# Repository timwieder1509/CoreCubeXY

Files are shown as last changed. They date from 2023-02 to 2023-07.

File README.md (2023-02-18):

# CoreCubeXY

### CoreCubeXY is a cheap and accessible Core-XY 3D printer

CoreCubeXY_rev2_v1_2023-Feb-13_05-33-34PM-000_CustomizedView17078552254_png

# Features:

Price: 250€-300€

All parts can be printed in PLA

Speeds of up to 300mm/s

Accelerations of up to 10000mm/s^2

Sensorless Homing when using TMC-Drivers  

Klicky_Probe compatible

Easy to upgrade 

tempImageiDoiUQ

Video of it printing a Benchy: https://youtu.be/joYZc8ANMAQ

***Note***

The 2020 extrusions I used are NUT 5 extrusions, that means that their slots are 5mm wide unlike on the more commonly on 3D printers used V-slot extrusions that have 6mm wide slots. 
You can use V-slot extrusions when you build one for yourself, use whatever is more easy for you to source. 
Just make sure that the hole in the middle of the profile has the correct diameter to cut an M5 thread into it. 

### ***Please note that this project is still a work in progress***

#### Coming Soon:

_A partlist/BOM_

_I'm already working on an alternative version with a single Z-Motor and mounts for conventional End-stops to make the build even more aproachable_

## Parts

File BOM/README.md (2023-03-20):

## Consider using the links provided in the BOM when you are building your own printer.
## That way you can support me without paying more. 
## Thanks ;)

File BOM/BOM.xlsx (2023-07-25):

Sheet: Printed Parts
3D Printed Parts
Part | amount | support needed
2xLM8UU_Mount_L | 1x | X
2xLM8UU_Mount_R | 1x
Idler_Mount_L | 1x
Idler_Mount_R | 1x
Motor_Mount_L | 1x | X
Motor_Mount_R | 1x | X
TR8_Mount | 2x
Z_Motor_Mount | 2x
AB_SB mount | 1x
Bed_Mount | 4x
Bed_Screw | 4x
Bed_Screw_Holder | 4x
Belt_Clamp | 1x
CCXY_Logo | 2x
Fan_Duct | 1x | X
Spacer | 4x
Foot | 4x
Gantry_Mount_L | 1x
Gantry_Mount_R | 1x
Hotend_Body | 1x | X
Klicky-Dock_Mount | 1x
Rod_Mount_bottom | 2x
Board_Mount | 1x
Rod_Mount_top | 2x

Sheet: Bought Parts
Bought Parts
Part | Amount | Link
Nema 17 Stepper Motor | 5x | https://bit.ly/42otSue
LM8UU | 4x | https://bit.ly/40k2tbb
SKR Mini E3 V2 | 1x | https://bit.ly/40mnx0S
GT2 Pulley | 2x | https://bit.ly/400JOBg
GT2 Idler | 10x | https://bit.ly/3FBs3QO
Mk8 Extruder | 1x | https://bit.ly/3n3rJEb
M5 x 8 | 50x | https://bit.ly/3yOAHbd
M3 x 25 | 50x | https://bit.ly/3lkwgSp
M3 x 8 | 50x | https://bit.ly/40jVfnr
M5 Hex-Nut | 10x
M3 Hex-Nut | 10x
M5 x 25 | 10x | https://bit.ly/3mTCXuP
M5 x 35 | 10x | https://bit.ly/403wvjG
Bondtech Extruder | 1x | https://bit.ly/40cFCyo
Linear shafts 8x200mm | 2x | https://bit.ly/3TupwO7
TR8 x 200 | 2x | https://bit.ly/3n7q8x0
4020 24v Fan | 1x | https://bit.ly/40g3odf
3010 24v Fan | 1x | https://bit.ly/3LDnOIE
5x8mm Shaft Coupler | 2x | https://bit.ly/40cGpPS
MGN9H (min 200mm/ max 250mm) | 2x | https://bit.ly/3JRuHEC
MGN12C 200mm | 1x | https://bit.ly/42mOvqO
Glas Bed 180x180 | 1x | https://bit.ly/40n2dIe
24v powersupply | 1x | https://bit.ly/401JMJF
M3 Heatset inserts | 20-30x | https://bit.ly/42sLghJ
255mm 2020 Extrusion | 12x | myaluprofil - Aluminum profile 20x20 Groove 5 I-Type (https://www.myaluprofil.de/product_info.php?no_boost=1)
180mm 2020 Extrusion | 4 | myaluprofil - Aluminum profile 20x20 Groove 5 I-Type (https://www.myaluprofil.de/product_info.php?no_boost=1)
M3 T-nuts | 40x | https://bit.ly/3qbo0WZ
M5 T-nuts | 40x | https://bit.ly/44A0dPw

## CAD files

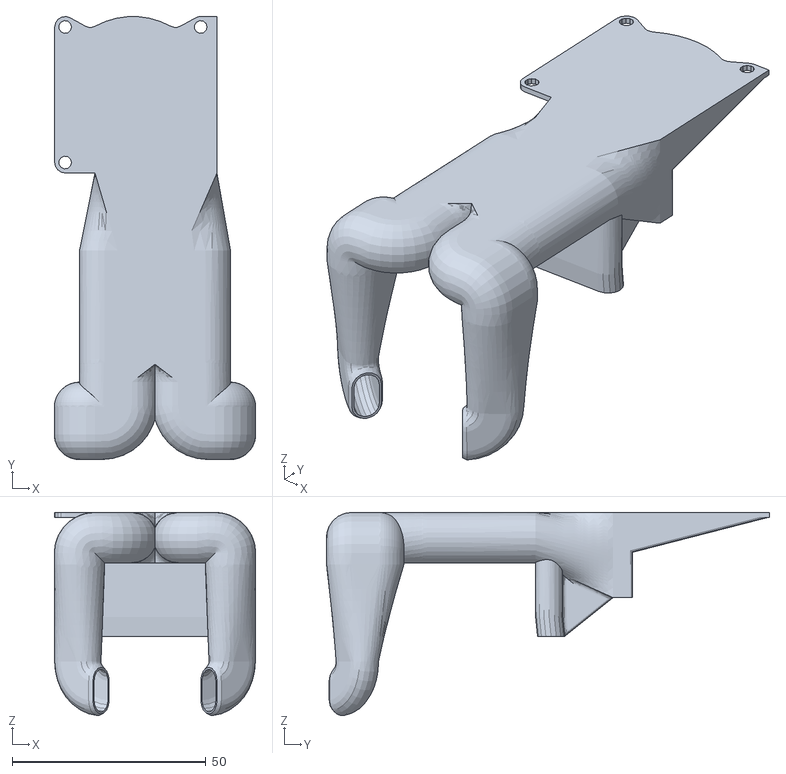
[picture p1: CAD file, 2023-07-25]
STL/Fan_Duct_v2.stl
52.0 x 114.4 x 52.5

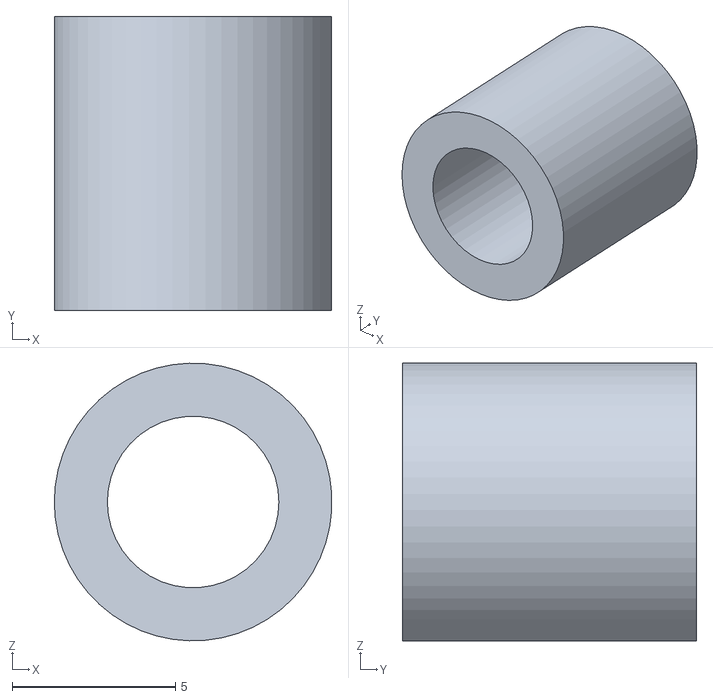
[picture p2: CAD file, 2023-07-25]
STL/Spacer.stl
8.49 x 9.00 x 8.50

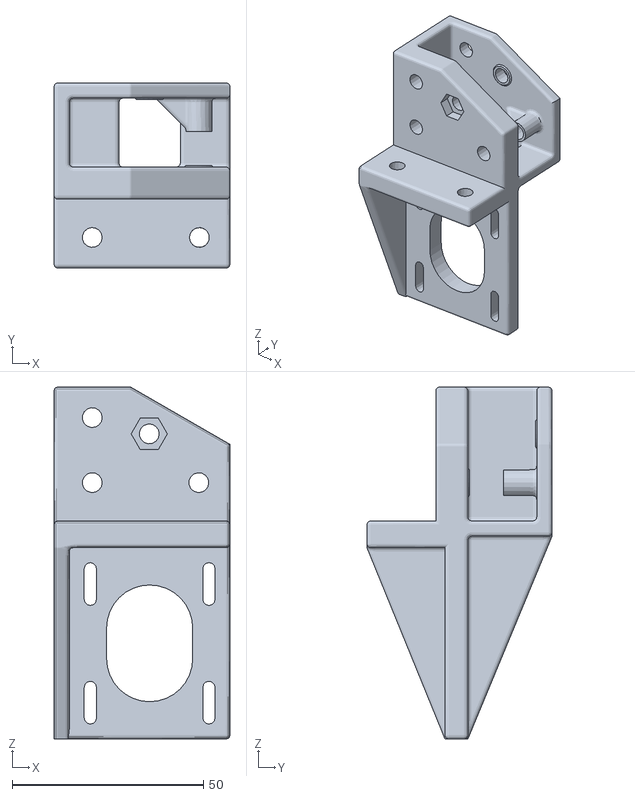
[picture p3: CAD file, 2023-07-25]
STL/Motor_Mount_L.stl
46.0 x 48.4 x 92.0

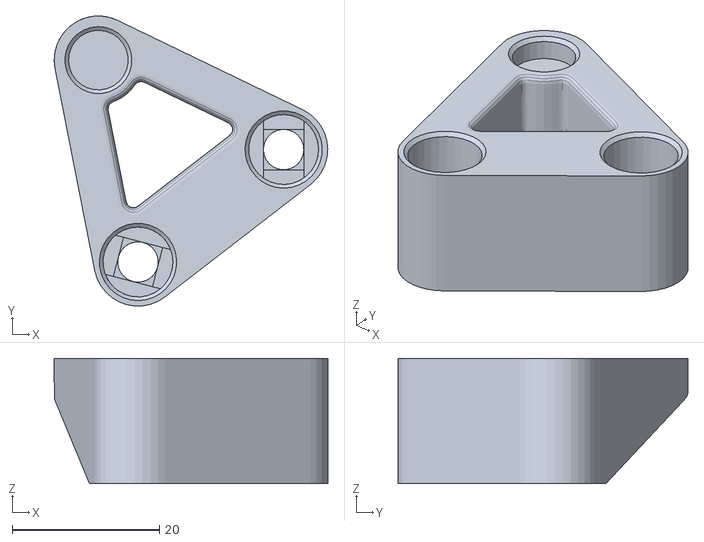
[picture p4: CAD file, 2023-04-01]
STL/Rod_Mount_bottom.stl
37.2 x 39.4 x 17.0

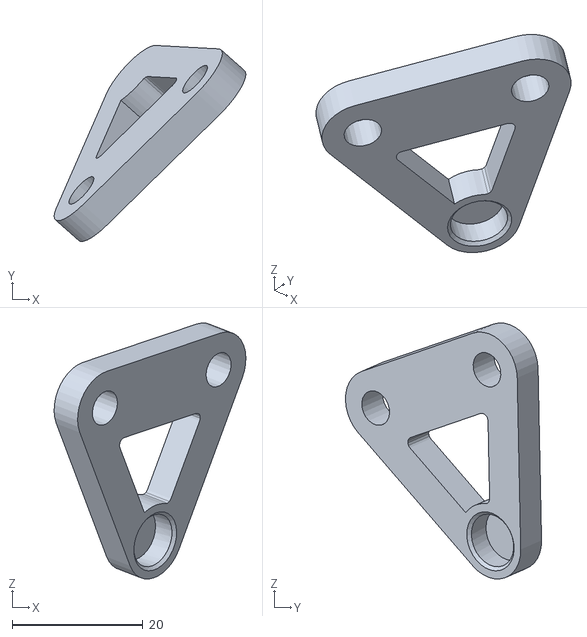
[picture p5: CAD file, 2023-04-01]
STL/Rod_Mount_top.stl
29.3 x 30.0 x 39.1

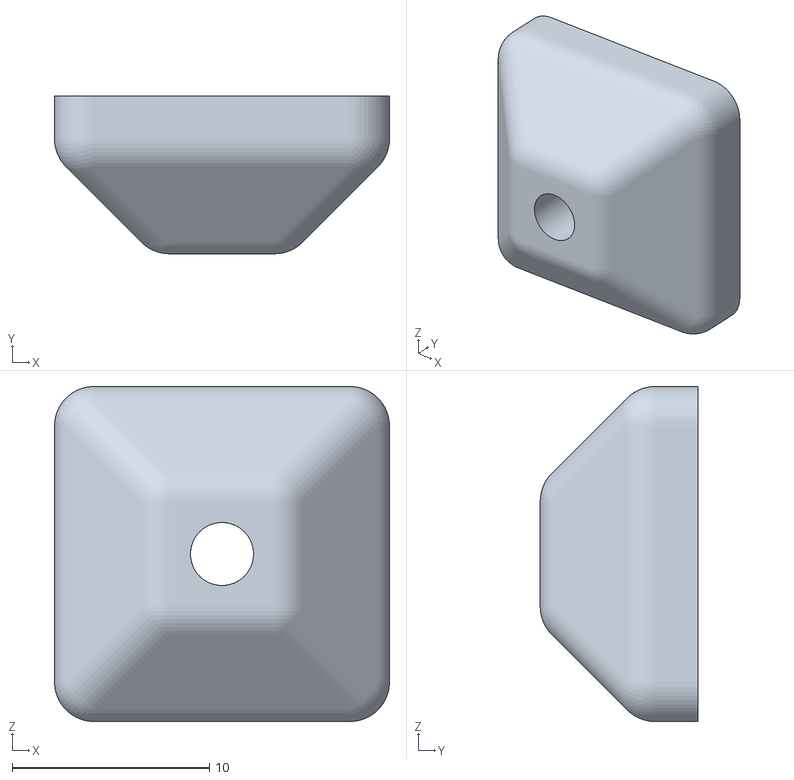
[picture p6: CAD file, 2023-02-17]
STL/Bed_Mount.stl
17.0 x 8.00 x 17.0

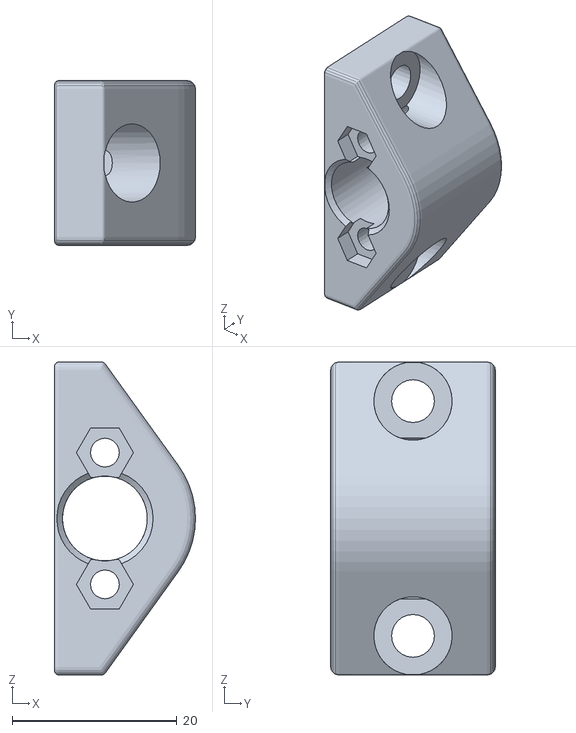
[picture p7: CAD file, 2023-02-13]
STL/TR8_Mount.stl
17.1 x 20.0 x 38.0

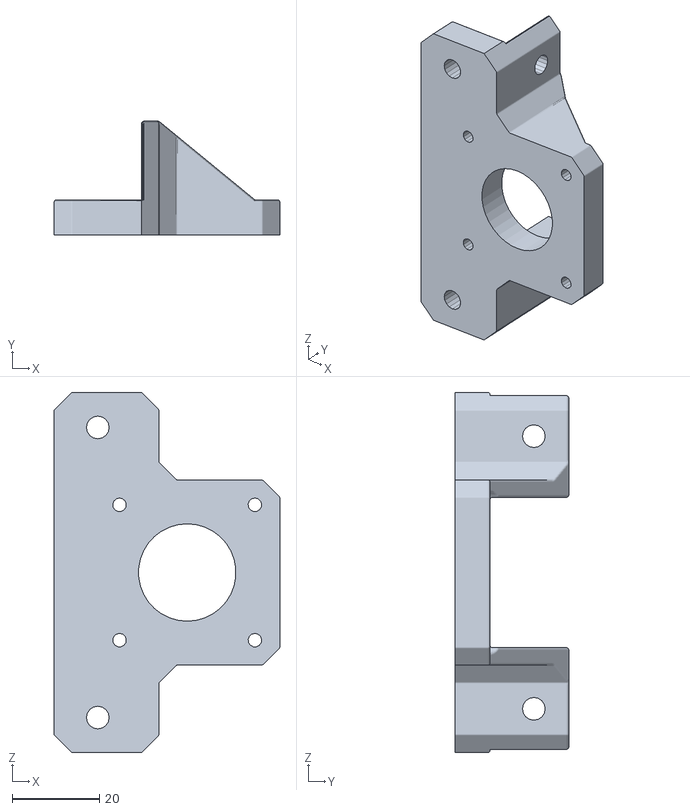
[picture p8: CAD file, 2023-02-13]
STL/Z_Motor_Mount.stl
51.7 x 26.0 x 82.4

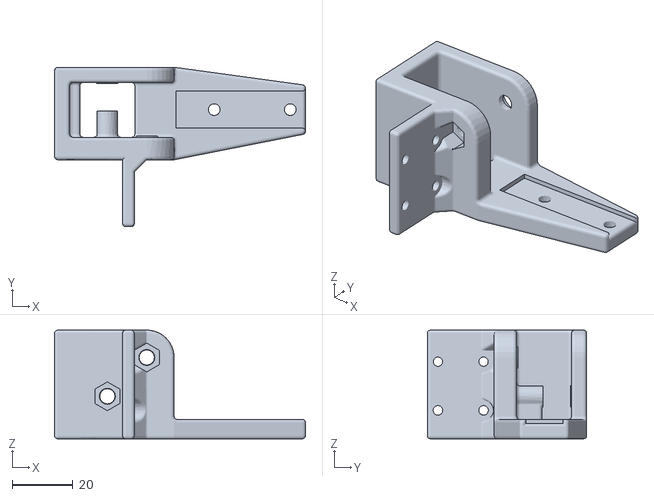
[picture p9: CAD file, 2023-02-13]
STL/Gantry_Mount_L.stl
82.5 x 52.4 x 35.7

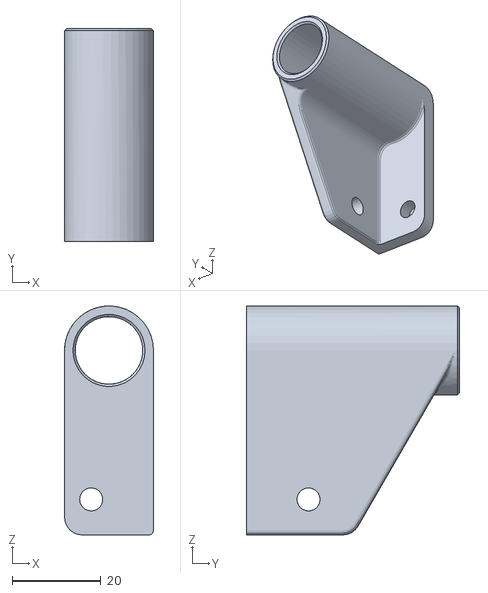
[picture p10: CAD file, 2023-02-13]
STL/2xLM8UU_Mount_R.stl
20.0 x 48.0 x 51.5

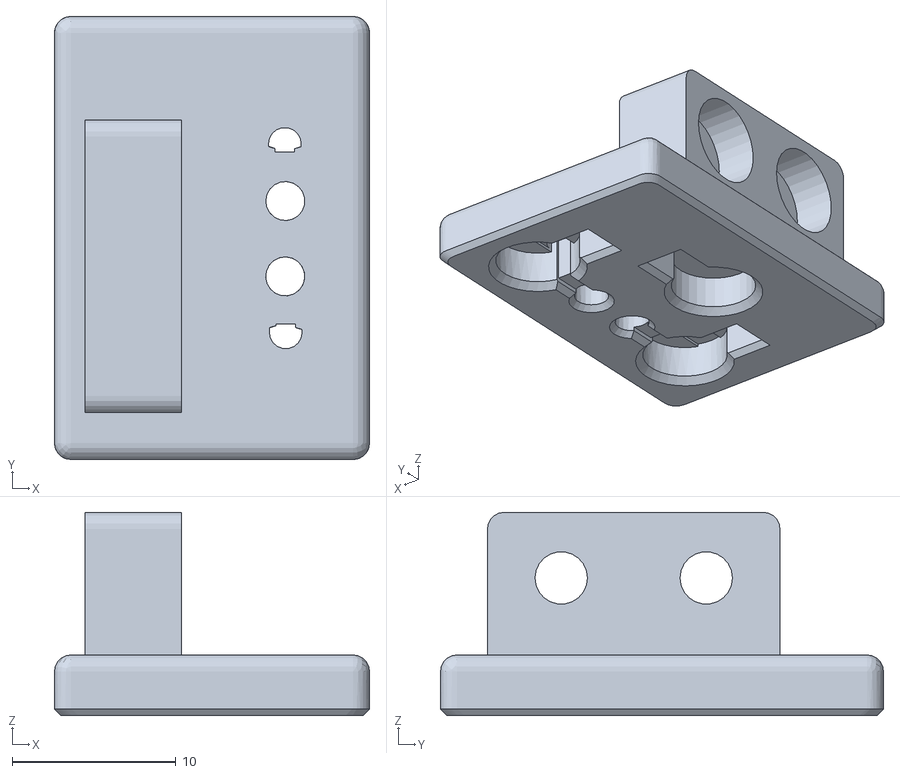
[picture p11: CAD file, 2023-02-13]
STL/AB_SB mount.stl
19.2 x 27.0 x 12.4

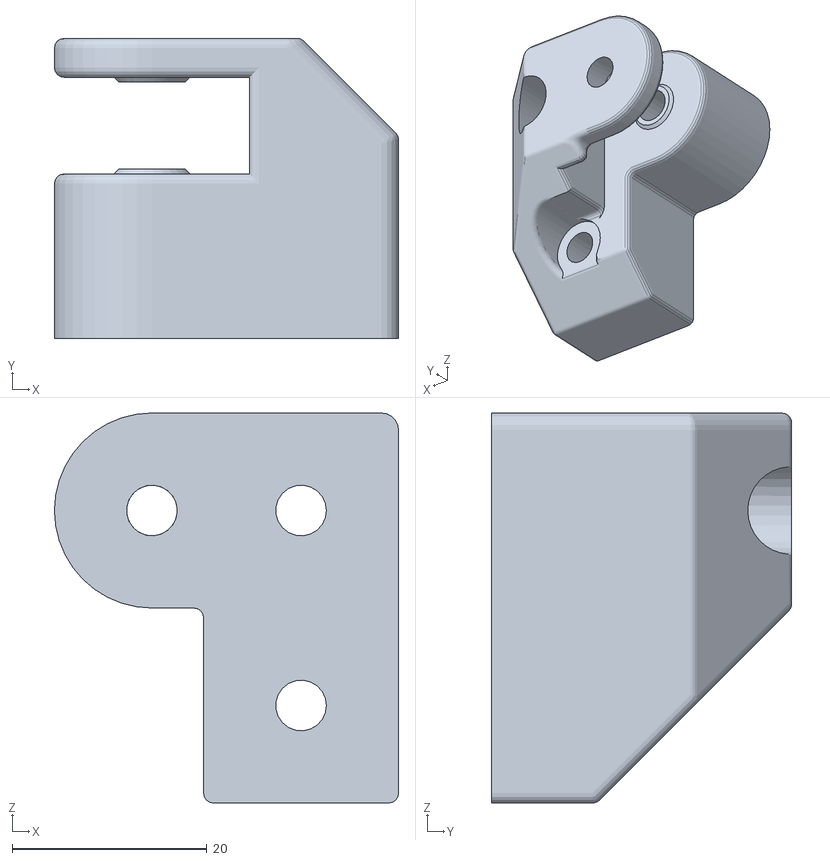
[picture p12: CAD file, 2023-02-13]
STL/Idler_Mount_R.stl
35.3 x 30.8 x 40.0

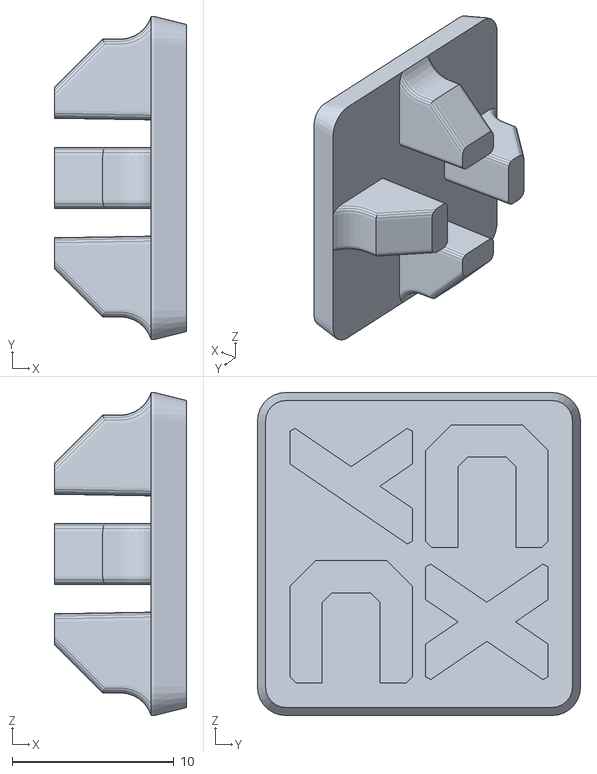
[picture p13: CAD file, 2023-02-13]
STL/CCXY_Logo.stl
8.20 x 20.0 x 20.0

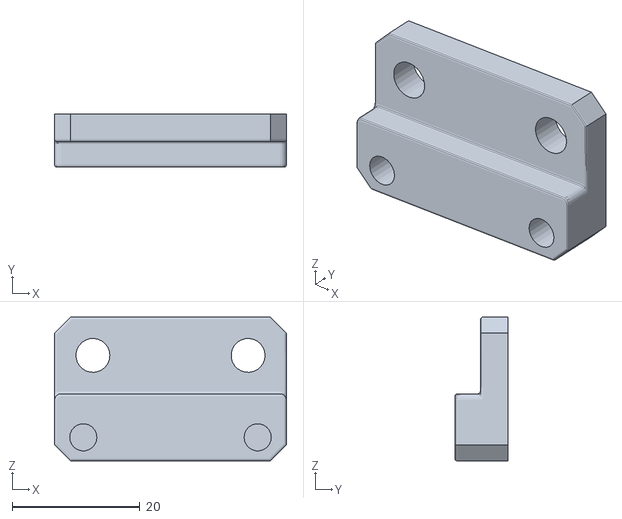
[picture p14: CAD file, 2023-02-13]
STL/Klicky-Dock_Mount.stl
36.3 x 8.35 x 22.5

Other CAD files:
STL/Motor_Mount_R.stl
STL/Gantry_Mount_R.stl
STL/Hotend_Body.stl
STL/2xLM8UU_Mount_L.stl
STL/Bed_Screw.stl
STL/Bed_Screw_Holder.stl
STL/Belt_Clamp.stl
STL/Fan_Duct.stl
STL/Foot.stl
STL/Idler_Mount_L.stl

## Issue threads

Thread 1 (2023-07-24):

Motor mounts in CAD as well as exported STL are not usable due to a section that blocks belt path

sakitume, 2023-07-24:
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

If you look at the video, you'll see the belt on let side goes from left/front idler all the way through the motor mount onto the pulley on the motor. The motor mount is different in the video compared to the one provided as an exported `.stl` as well as what is in the `.step` file.

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

sakitume, 2023-07-24:
I don't know if this is a real issue or not, but I couldn't understand how the belt would be able to run from the front idler to the motor pulley. So I removed that piece and made a separate spacer with an OD of 8mm and an ID of 5.4mm and is 8.2mm tall. I will use a 0.5mm shim between the spacer and the pulley so that it can spin freely without binding against the spacer.

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

After I print out the new pieces I will let you know if that worked for me or not.

timwieder1509, 2023-07-24:
Hi,

Yes you are right, i have to change that, it seems like i have uploaded an old version of this part. Thanks for letting me know! I also worked with separate spacers on my printer.
________________________________
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

sakitume, 2023-07-24:
Ah, thanks for confirming. The spacer I made seems to be a good fit (in conjunction with the 0.5mm shim I have). I'll know for sure once I'm able to actually tension the belts.

I've said this a few times, but I really like the belt pathing you've chosen and how you're able to reduce the pulley count to the bare minimum; similar designs I've come across need two additional pulleys per motor.

Really looking forward to testing out the X/Y motion system soon.

timwieder1509, 2023-07-25:
Thank you for your comment and the positive response to my project. I very am glad to see that you like my design. I fixed the issue and added a spacer to the files.

Closed 2023-07-25.

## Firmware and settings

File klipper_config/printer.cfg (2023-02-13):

# This file contains common pin mappings for the BIGTREETECH SKR mini
# E3 v2.0. To use this config, the firmware should be compiled for the
# STM32F103 with a "28KiB bootloader" and USB communication. Also,
# select "Enable extra low-level configuration options" and configure
# "GPIO pins to set at micro-controller startup" to "!PA14".

# The "make flash" command does not work on the SKR mini E3. Instead,
# after running "make", copy the generated "out/klipper.bin" file to a
# file named "firmware.bin" on an SD card and then restart the SKR
# mini E3 with that SD card.

# See docs/Config_Reference.md for a description of parameters.

[include mainsail.cfg]

[stepper_x]
step_pin: PB13
dir_pin: !PB12
enable_pin: !PB14
microsteps: 16
rotation_distance: 40
position_endstop: 160
endstop_pin: tmc2209_stepper_x:virtual_endstop
homing_retract_dist: 0
position_max: 160
homing_speed: 30

[tmc2209 stepper_x]
diag_pin: ^PC0
uart_pin: PC11
tx_pin: PC10
uart_address: 0
run_current: 0.580
stealthchop_threshold: 999999
driver_SGTHRS: 67  # 255 is most sensitive value, 0 is least sensitive

[stepper_y]
step_pin: PB10
dir_pin: !PB2
enable_pin: !PB11
microsteps: 16
rotation_distance: 40
endstop_pin: tmc2209_stepper_y:virtual_endstop
homing_retract_dist: 0
position_endstop: 165
position_max: 165
homing_speed: 30

[tmc2209 stepper_y]
diag_pin: ^PC1
uart_pin: PC11
tx_pin: PC10
uart_address: 2
run_current: 0.580
stealthchop_threshold: 999999
driver_SGTHRS: 100  # 255 is most sensitive value, 0 is least sensitive

[stepper_z]
step_pin: PB0
dir_pin: PC5
enable_pin: !PB1
microsteps: 16
rotation_distance: 8
endstop_pin: probe:z_virtual_endstop
#position_endstop: 0.0
position_max: 130

[tmc2209 stepper_z]
uart_pin: PC11
tx_pin: PC10
uart_address: 1
run_current: 0.580
stealthchop_threshold: 999999

[probe]
probe_pin: PC2
x_offset: 0
y_offset: 19.75
z_offset: 0



[extruder]
step_pin: PB3
dir_pin: !PB4
enable_pin: !PD2
microsteps: 16
rotation_distance: 33.500
nozzle_diameter: 0.400
filament_diameter: 1.750
heater_pin: PC8
sensor_type: EPCOS 100K B57560G104F
sensor_pin: PA0
control: pid
pid_Kp: 21.527
pid_Ki: 1.063
pid_Kd: 108.982
min_temp: 0
max_temp: 250

[tmc2209 extruder]
uart_pin: PC11
tx_pin: PC10
uart_address: 3
run_current: 0.650
stealthchop_threshold: 999999

#[heater_bed]
#heater_pin: PC9
#sensor_type: ATC Semitec 104GT-2
#sensor_pin: PC3
#control: pid
#pid_Kp: 54.027
#pid_Ki: 0.770
#pid_Kd: 948.182
#min_temp: 0
#max_temp: 130

[heater_fan heatbreak_cooling_fan]
pin: PC7

[fan]
pin: PC6

[mcu]
serial: /dev/serial/by-id/usb-Klipper_stm32f103xe_39FFD8053041543727722343-if00

[printer]
kinematics: corexy
max_velocity: 300
max_accel: 3000
max_z_velocity: 5
max_z_accel: 100

[static_digital_output usb_pullup_enable]
pins: !PA14

[board_pins]
aliases:
    # EXP1 header
    EXP1_1=PB5,  EXP1_3=PA9,   EXP1_5=PA10, EXP1_7=PB8,  EXP1_9=<GND>,
    EXP1_2=PA15, EXP1_4=<RST>, EXP1_6=PB9,  EXP1_8=PB15, EXP1_10=<5V>

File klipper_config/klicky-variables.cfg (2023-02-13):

# This macro was provided by discord user Garrettwp to whom i give my thanks for sharing it with me.
# I have tweaked it a lot.
# They are based on the great Annex magprobe dockable probe macros "#Originally developed by Mental,
# modified for better use on K-series printers by RyanG and Trails", kudos to them.
# That macro as since evolved into a klipper plugin that currently is pending inclusion in klipper,
# more information here, https://github.com/Annex-Engineering/Quickdraw_Probe/tree/main/Klipper_Macros
# User richardjm revised the macro variables and added some functions, thanks a lot
# by standing on the shoulders of giants, lets see if we can see further
#
# the current home for this version is https://github.com/jlas1/Klicky-Probe
# the 1000 values below is to give an error instead of doing something wrong, hopefully, this won't be used is a printer larger than 1 meter

[gcode_macro _User_Variables]
variable_verbose:             True    # Enable verbose output
variable_debug:              False    # Enable Debug output
variable_travel_speed:         250    # how fast all other travel moves will be performed when running these macros
variable_move_accel:          4000    # how fast should the toolhead accelerate when moving
variable_dock_speed:            50    # how fast should the toolhead move when docking the probe for the final movement
variable_release_speed:         75    # how fast should the toolhead move to release the hold of the magnets after docking
variable_z_drop_speed:          20    # how fast the z will lower when moving to the z location to clear the probe

variable_safe_z:         	    10    # Minimum Z for attach/dock and homing functions
# if true it will move the bed away from the nozzle when Z is not homed
variable_enable_z_hop:        True    # set this to false for beds that fall significantly under gravity (almost to Z max)

variable_max_bed_y:            140    # maximum Bed size avoids doing a probe_accuracy outside the bed
variable_max_bed_x:            155    # maximum Bed size avoids doing a probe_accuracy outside the bed

# if a separate Z endstop switch is in
# use, specify the coordinates of the switch here (Voron).
# Set to 0 to have the probe move to center of bed
variable_z_endstop_x:            0
variable_z_endstop_y:            0

#Check the printer specific documentation on klipper Dock/Undock configuration, these are dummy values
#dock location
variable_docklocation_x:         0    # X Dock position
variable_docklocation_y:       -20    # Y Dock position
variable_docklocation_z:      -128    # Z dock position (-128 for a gantry/frame mount)

#The following variables are used if the dock is deployed and retracted via a servo motor
variable_enable_dock_servo:  False    # Set to true if your klicky dock is servo-controlled
variable_servo_name:        'NAME'    # The name of the dock servo defined in printer.cfg under [servo]
variable_servo_deploy:          10    # This EXAMPLE is the value used to deploy the servo fully
variable_servo_retract:         11    # This EXAMPLE is the value used to retract the servo fully (initial_angle in [servo] config)
variable_servo_delay:          250    # This is a delay to wait the servo to reach the requested position, be carefull with high values

#Dock move, final toolhead movement to release the probe on the dock
#it's a relative move
Variable_dockmove_x:            40
Variable_dockmove_y:             0
Variable_dockmove_z:             0

#Attach move. final toolhead movement to attach the probe on the mount
#it's a relative move
Variable_attachmove_x:           0
Variable_attachmove_y:         -20
Variable_attachmove_z:           0

#Umbilical to help untangle the umbilical in difficult situations
variable_umbilical:          False    # should we untangle the umbilical
variable_umbilical_x:           15    # X umbilical position
variable_umbilical_y:           15    # Y umbilical position

# location to park the toolhead
variable_park_toolhead:       True    # Enable toolhead parking
variable_parkposition_x:      77.5
variable_parkposition_y:        80
variable_parkposition_z:        10    # -128 excludes Z - Park only on X-Y

variable_version:                1    # Helps users to update the necessary variables, do not update if the variables above are not updated

#Below this remark, you normally do not need to configure
#Attach move2
Variable_attachmove2_x:          0    # intermediate toolhead movement to attach
Variable_attachmove2_y:          0    # the probe on the dock
Variable_attachmove2_z:          0    # (can be negative)

variable_home_backoff_x:        10    # how many mm to move away from the X endstop after homing X
                                      # this is useful for the voron v0 to enable the toolhead to move out of the way to allow an unstricted Y homing
variable_home_backoff_y:        10    # how many mm to move away from the Y endstop after homing Y

variable_override_homing:       ''    # configures what axis to home first
                                      #  '' = default klicky behavior (tries to avoid the hitting the dock)
                                      # 'X' = forces X to home first
                                      # 'Y' = forces Y to home first
                                      
variable_dock_on_zhome:       True    # docks the probe on Z Homing if not necessary (avoids hitting the bed on some printers       

variable_bypass_probe_docking:        False                               

# Do not modify below
gcode:
    {% set Mx = printer['configfile'].config["stepper_x"]["position_max"]|float %}
    {% set My = printer['configfile'].config["stepper_y"]["position_max"]|float %}
    {% set Ox = printer['configfile'].config["probe"]["x_offset"]|float %}
    {% set Oy = printer['configfile'].config["probe"]["y_offset"]|float %}
    {% set Oz = printer['configfile'].config["probe"]["z_offset"]|float %}

    # If x, y coordinates are set for z endstop, assign them
    {% if z_endstop_x != 0 or z_endstop_y != 0 %}
        SET_GCODE_VARIABLE MACRO=_Probe_Variables VARIABLE=z_endstop_x VALUE={ z_endstop_x }
        SET_GCODE_VARIABLE MACRO=_Probe_Variables VARIABLE=z_endstop_y VALUE={ z_endstop_y }

    # if no x, y coordinates for z endstop, assume probe is endstop and move toolhead to center of bed
    {% else %}
        SET_GCODE_VARIABLE MACRO=_Probe_Variables VARIABLE=z_endstop_x VALUE={ (Mx * 0.5) - Ox }
        SET_GCODE_VARIABLE MACRO=_Probe_Variables VARIABLE=z_endstop_y VALUE={ (My * 0.5) - Oy }
    {% endif %}

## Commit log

2023-03-20 Create BOM
2023-07-24 Delete Motor_Mount_L.stl
    A new version of this part will be uploaded in the next few days. Please don't print the old version in case you have already downloaded it.
    [Motor_Mount_L.stl]
2023-07-24 Delete Motor_Mount_R.stl
    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
    [Motor_Mount_R.stl]
2023-07-24 Delete CoreCubeXY_dual-Z_v2.stp
    A new version will be uploaded in the next few days, as the old one had a problem concerning the belt routing.
2023-07-25 Create CAD
